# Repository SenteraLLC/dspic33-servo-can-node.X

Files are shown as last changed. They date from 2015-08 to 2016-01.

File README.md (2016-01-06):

# CAN Servo-Node

Initial development performed by partnership of [Sentera, LLC](https://sentera.com/) and [University of Minnesota](http://www.uav.aem.umn.edu/).

## System Overview
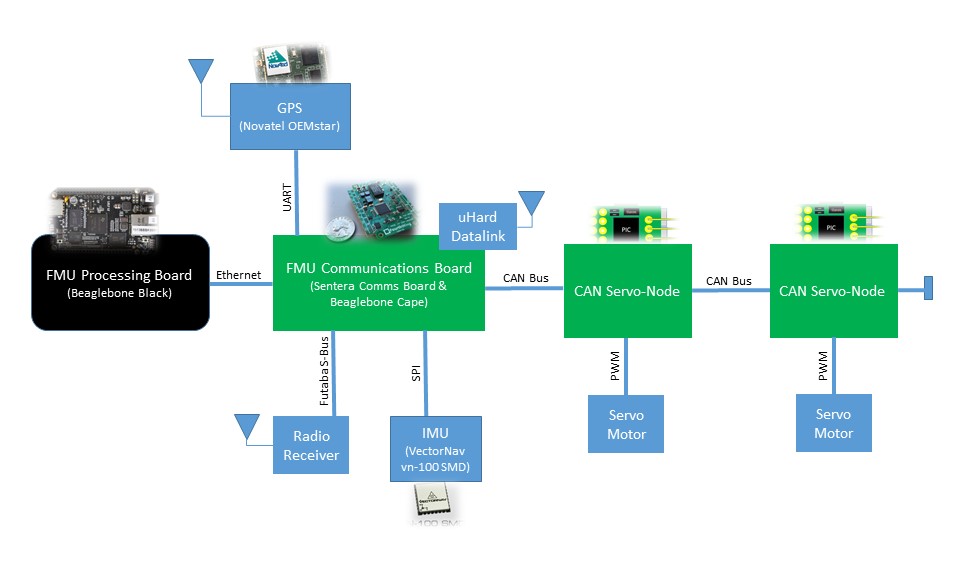
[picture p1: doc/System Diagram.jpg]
System Diagram


The CAN Servo-Node is designed as a component of the Flight Management System.  The CAN Servo-Node is a Microchip dsPIC33 based module with the primary function of receiving servo commands over a CAN bus, and controlling power to a servo based on those commands.  CAN communication is documented in file [UMN FMU Communication Protocol](https://github.com/SenteraLLC/pic32-fmu.X/blob/master/doc/UMN%20FMU%20Communication%20Protocol.docx).  When commanding the position of a servo, the software performs servo calibration correction so the required PWM value is applied to the servo.

Besides the described primary function, the CAN Servo-Node also:

* Performs monitoring of servo current and voltage, and annunciation of servo status on the CAN bus.

* Performs monitoring of VSENSE1 and VSENSE2 signals (described more below), calibration correction of values, and annunciation on the CAN bus.

* Provides reading and writing of calibration correction values (for the servo, VSENSE1, and VSENSE2) on the CAN bus.

The software design for the FMU Communications Board can be found at GitHub repository: [https://github.com/SenteraLLC/pic32-fmu.X](https://github.com/SenteraLLC/pic32-fmu.X).

## Project Folder Structure
The project includes the following folders:

>[doc](/doc) - documentation for the project.

>[doxygen](/doxygen) - project file for generating Doxygen documentation.

>[hw](/hw) - hardware design schematics.

>[inc](/inc) - include (i.e. header) code files.

>[ipe](/ipe) - instructions for a device programming method which maintains unique serial numbers.

>[nbproject](/nbproject) - MPLAB X IDE project files.

>[src](/src) – source code files.

## Hardware Overview
The hardware contains the following connectors:

>J1 - Servo voltage input (note: PWM input not currently used).

>J2 - Servo voltage and PWM output.

>J3 - Power (VCC/GND) and CAN connector.

>J4 - Duplicate Power (VCC/GND) and CAN connector.

>J5 - Power (VCC/GND) output and V_SENSE1 input.

>J6 - Power (VCC/GND) output and V_SENSE2 input.

The J3 or J4 connector is used to supply power to the CAN Servo-Node and to provide connection to the CAN bus.  The duplicate connector is used to continue wiring to additional devices (e.g. an additional CAN Servo-Node) or to provide termination of the CAN bus (i.e. terminating resistor).

The J5 and J6 connectors provide power to two additional devices.  These connectors also include an analog signal (V_SENSE1/2) which the CAN Servo-Node reads.  Likely devices connected to this interface include pressure sensors, temperature sensors, potentiometers, etc.

*Note: The CAN Servo-Node requires 5V supplied power (VCC) through the J3 or J4 connector.*

## Software Overview
All source code is commented using Doxygen style formatting.  Therefore, Doxygen can be used to generate an easily navigable document which provides greater detail into the software's operation than the overview which is provided here.

### Software Executive
The software implements a preemptive, cyclic executive using four threads.  The software threads are:

1. **Reset**: Thread is executed following reset.  Within the MPLAB environment this is implemented as "main" which provides C-environment control-flow entry.

2. **10ms**: Thread is executed every 10ms and provides the primary periodic software processing.

3. **0.1ms**: Thread is executed every 0.1ms and provides a granular time reference for determining relative time.

4. **Default**: Thread is executed if any unexpected interrupts occur.

The 'Reset' thread is executed out of reset and has the lowest priority.  The '10ms' thread has a priority of 1 and therefore can preempt the 'Reset' thread.  The '0.1ms' thread has a priority of 2 and therefore can preempt both the 'Reset' and '1ms' threads.

### Software Modules
The software is a modular design with no global data access.  The software modules are explained below, and map directly to [source code](/src) file names:

>**adc**: Analog to Digital Converter (ADC) driver.

>**can**: Controller Area Network (CAN) driver.

>**cfg**: Management of configuration data used by the software.  Note: configuration data is readable and writeable through the CAN interface.

>**dio**: Discrete I/O driver.

>**i2c**: Inter-Integrated Circuit (I2C) driver.

>**ina219**: External current/power monitor (INA219) driver.

>**main**: Software executive and C-environment control-flow entry.

>**nvm**: Non-Volatile Memory (NVM) driver.

>**osc**: Oscillator (OSC) driver.

>**pwm**: Pulse-Width Modulation (PWM) driver.

>**rst**: Reset condition detection.  The reset condition is annunciated over the CAN bus so unexpected resets can be identified.

>**servo**: Received CAN messages are processed to determine the servo control type - position or PWM control.  For position control, servo calibration correction is performed.  The determined PWM value is output to the servo and servo status CAN messages are periodically transmitted.

>**tmr**: Timer (TMR) driver.

>**util**: Utility functions.

>**ver**: Version and identification management. Version CAN messages are periodically transmitted to provide node identification.

>**vsense**: VSENSE1/2 signal management. The signals are calibration corrected and their value periodically annunciated in a CAN message.

>**wdt**: Watchdog Timer (WDT) driver.

## Building the Software
The recommended method for building the software is using tool [MPLAB X IDE](http://www.microchip.com/mplabx/) with compiler [MPLAB XC16](http://www.microchip.com/xc16/).  The IDE and compiler are both free software provided by Microchip.

*Note: v3.0 of MPLAB X IDE was used during development.*

*Note: v1.24 of MPLAB XC16 was used during development.*

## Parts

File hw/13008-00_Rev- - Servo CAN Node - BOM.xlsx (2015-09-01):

Production Quantity: | 25
Designator | Fitted | Comment | Manufacturer Part Number 1 | Manufacturer 1 | Description | Value | Quantity | Supplier 1 | Supplier Part Number 1 | Supplier Unit Price 1 | Supplier Order Qty 1 | Supplier Stock 1 | Delta Supplier 1 | Supplier Subtotal 1
C3, C4, C5, C7, C8, C9 | Fitted | C1005X7R1H104K | C1005X7R1H104K050BB | TDK Corporation | CAP CER 0.1UF 50V 10% X7R 0402 | 0.1uF | 6 | Digi-Key | 445-5932-1-ND | $0.05 | 150 | 7974509 | 7974359 | $7.12
C6 | Fitted | C1608X5R1A106M | C1608X5R1A106M080AC | TDK Corporation | CAP CER 10UF 10V X5R 20% 0603 | 10uF | 1 | Digi-Key | 445-6853-1-ND | $0.39 | 25 | 1201382 | 1201357 | $9.82
J1, J2 | Fitted | TSW-103-25-F-S-RA | TSW-103-25-F-S-RA | Samtec Inc | CONN HEADER 3POS .100" R/A AU |  | 2 | Digi-Key | TSW-103-25-F-SRA-ND | $0.46 | 50 | 0 | -50 | $23.00
J3, J4 | Fitted | 502386-0470 | 5023860470 | Molex Inc | CLIK-Mate CONN RCPT 4POS 1.25MM R/A SMD |  | 2 | Digi-Key | WM4948CT-ND | $0.96 | 50 | 3060 | 3010 | $48.23
J5, J6 | Fitted | 502386-0370 | 5023860370 | Molex Inc | CONN RCPT 3POS 1.25MM R/A SMD |  | 2 | Digi-Key | WM4947CT-ND | $0.88 | 50 | 1588 | 1538 | $44.07
J7 | Fitted | 502386-0570 | 5023860570 | Molex Inc | CLIK-Mate CONN RCPT 5POS 1.25MM R/A SMD |  | 1 | Digi-Key | WM4949CT-ND | $1.11 | 25 | 9764 | 9739 | $27.72
R2, R6, R8 | Fitted | ERJ-2RKF3300X | ERJ-2RKF3300X | Panasonic Electronic Components | RES 330 OHM 1/10W 1% 0402 SMD | 330 | 3 | Digi-Key | P330LCT-ND | $0.01 | 100 | 665642 | 665542 | $1.10
R3, R4 | Fitted | ERJ-2RKF3301X | ERJ-2RKF3301X | Panasonic Electronic Components | RES 3.30K OHM 1/10W 1% 0402 SMD | 3.3k | 2 | Digi-Key | P3.30KLCT-ND | $0.01 | 50 | 391761 | 391711 | $0.75
R5 | Fitted | ERJ-2RKF1002X | ERJ-2RKF1002X | Panasonic Electronic Components | RES 10.0K OHM 1/10W 1% 0402 SMD | 10k | 1 | Digi-Key | P10.0KLCT-ND | $0.01 | 50 | 13048611 | 13048561 | $0.75
R7 | Fitted | PMR10EZPFU8L00 | PMR10EZPFU8L00 | Rohm Semiconductor | RES SMD 0.008 OHM 1% 1/2W 0805 | .008 | 1 | Digi-Key | RHM.008AJCT-ND | $0.45 | 25 | 8069 | 8044 | $11.14
U1 | Fitted | SN65HVD1050DR | SN65HVD1050DR | Texas Instruments | IC EMC CAN TRANSCEIVER 8-SOIC |  | 1 | Digi-Key | 296-26335-1-ND | $1.03 | 25 | 11992 | 11967 | $25.75
U2 | Fitted | INA219BIDCNT | INA219BIDCNT | Texas Instruments | IC MONITOR PWR/CURR BID SOT-23-8 |  | 1 | Digi-Key | 296-27898-1-ND | $2.36 | 25 | 2367 | 2342 | $59.00
U3 | Fitted | KC5032A10.0000CMGE00 | KC5032A10.0000CMGE00 | AVX Corp/Kyocera Corp | OSCILLATOR XO 10.000MHZ CMOS SMD |  | 1 | Digi-Key | 1253-1284-1-ND | $1.49 | 25 | 1323 | 1298 | $37.30
U4 | Fitted | DSPIC33EV256GM102-I/MM | DSPIC33EV256GM102-I/MM | Microchip Technology | IC DSC 16BIT 16KB |  | 1 | Digi-Key | DSPIC33EV256GM102-I/MM-ND | $4.43 | 25 | 184 | 159 | $110.75
R1 | Not Fitted | ERJ-2RKF1200X | ERJ-2RKF1200X | Panasonic Electronic Components | RES 120 OHM 1/10W 1% 0402 SMD | 120 | 0 | Digi-Key | P120LCT-ND | $0.10 | 1 | 185622 | 185621 | $0.10
 |  |  |  |  |  |  | 25 |  |  |  |  |  |  | $406.61
 |  |  |  |  |  |  |  |  |  |  |  |  | Unit Cost | $16.26

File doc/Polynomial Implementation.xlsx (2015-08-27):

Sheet: Servo
 | Multiplier | Bit Shift
Coeff Mul | 100000000
Val Mul | 1000
Calc Mul | 1000000000
Out Mul | 1000000
Calc | 1073741824 | 30
 | 100
 | type | min supported | max supported |  | unit | Scale |  | decimal | integer (number) | integer (scientific)
c0 | int32_t | -2147483648 | 2147483647 |  | [s] |  | 1E8 | 0.00000000 | 0 | 0
c1 | int32_t | -2147483648 | 2147483647 |  | [s/rad^1] |  | 1E8 | 0.00100000 | 100000 | 100000
c2 | int32_t | -2147483648 | 2147483647 |  | [s/rad^2] |  | 1E8 | 0.00001600 | 1600 | 1600
c3 | int32_t | -2147483648 | 2147483647 |  | [s/rad^3] |  | 1E8 | 0.00000000 | 0 | 0
c4 | int32_t | -2147483648 | 2147483647 |  | [s/rad^4] |  | 1E8 | 0.00000000 | 0 | 0
c5 | int32_t | -2147483648 | 2147483647 |  | [s/rad^5] |  | 1E8 | 0.00000000 | 0 | 0
x | int16_t | -32768 | 32767 |  | [rad] |  | 1E3 | 0.25 | 250 | 250
x_calc | int64_t | -9.223372037e+18 | 9.223372037e+18 |  | [rad] |  | 2^30 | 0.250 | 268435456 | 268435456 |  | Up-scaled for calculation resolution.
x_calc^0 | int32_t | -2147483648 | 2147483647 |  |  |  | 2^30 | 1.000000000 | 1073741824 | 1073741824
x_calc^1 | int32_t | -2147483648 | 2147483647 |  | [rad^1] |  | 2^30 | 0.250000000 | 268435456 | 268435456
x_calc^2 | int32_t | -2147483648 | 2147483647 |  | [rad^2] |  | 2^30 | 0.062500000 | 67108864 | 67108864
x_calc^3 | int32_t | -2147483648 | 2147483647 |  | [rad^3] |  | 2^30 | 0.015625000 | 16777216 | 16777216
x_calc^4 | int32_t | -2147483648 | 2147483647 |  | [rad^4] |  | 2^30 | 0.003906250 | 4194304 | 4194304
x_calc^5 | int32_t | -2147483648 | 2147483647 |  | [rad^5] |  | 2^30 | 0.000976562 | 1048576 | 1048576
c0*x^0 | int64_t | -9.223372037e+18 | 9.223372037e+18 |  | [s] |  | 1E8 * 2^30 | 0.000000000 | 0 | 0
c1*x^1 | int64_t | -9.223372037e+18 | 9.223372037e+18 |  | [s] |  | 1E8 * 2^30 | 0.000250000 | 26843545600000 | 26843545600000
c2*x^2 | int64_t | -9.223372037e+18 | 9.223372037e+18 |  | [s] |  | 1E8 * 2^30 | 0.000001000 | 107374182400 | 107374182400
c3*x^3 | int64_t | -9.223372037e+18 | 9.223372037e+18 |  | [s] |  | 1E8 * 2^30 | 0.000000000 | 0 | 0
c4*x^4 | int64_t | -9.223372037e+18 | 9.223372037e+18 |  | [s] |  | 1E8 * 2^30 | 0.000000000 | 0 | 0
c5*x^5 | int64_t | -9.223372037e+18 | 9.223372037e+18 |  | [s] |  | 1E8 * 2^30 | 0.000000000 | 0 | 0
 |  |  |  |  |  |  |  |  | 25100
PWM | uint16_t | 0 | 65536 |  | [s] |  | 1E6 | 0.000251000 | 251 | 251
 |  |  |  | realterm
 |  |  |  |  |  |  |  | 16 |  |  | 2 | 8
 |  |  |  |  |  |  |  | 4 |  |  | *
 |  |  |  |  |  |  |  |  |  |  | 3 | 12
 |  |  |  |  |  |  |  |  |  |  |  | 96
 |  |  |  |  |  |  |  |  |  |  |  | 6

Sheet: VSENSE
 | Multiplier | Bit Shift
Val Mul | 262144 | 18
Coeff Mul | 10000
Calc | 1073741824 | 30 |  | Number represented in Q2.30 format (i.e. 30 fractional bits).
Out Mul | 100
 | type | min supported | max supported |  | Scale | Scale | decimal | integer (number) | integer (scientific)
c0 | int32_t | -2147483648 | 2147483647 |  | 1E4 | 10000 | 1.0000 | 10000 | 10000
c1 | int32_t | -2147483648 | 2147483647 |  | 1E4 | 10000 | 4.0000 | 40000 | 40000
c2 | int32_t | -2147483648 | 2147483647 |  | 1E4 | 10000 | 16.0000 | 160000 | 160000
c3 | int32_t | -2147483648 | 2147483647 |  | 1E4 | 10000 | 64.0000 | 640000 | 640000
c4 | int32_t | -2147483648 | 2147483647 |  | 1E4 | 10000 | 256.0000 | 2560000 | 2560000
c5 | int32_t | -2147483648 | 2147483647 |  | 1E4 | 10000 | 1024.0000 | 10240000 | 10240000
x | int16_t | -32768 | 32767 |  | 2^12 | 4096 | 0.2500000 | 1024 | 1024
x_calc | int32_t | -2147483648 | 2147483647 |  | 2^30 | 1073741824 | 0.2500000 | 268435456 | 268435456 | Up-scaled for calculation resolution.
x_calc^0 | int32_t | -2147483648 | 2147483647 |  | 2^30 | 1073741824 | 1.0000000 | 1073741824 | 1073741824
x_calc^1 | int32_t | -2147483648 | 2147483647 |  | 2^30 | 1073741824 | 0.2500000 | 268435456 | 268435456
x_calc^2 | int32_t | -2147483648 | 2147483647 |  | 2^30 | 1073741824 | 0.0625000 | 67108864 | 67108864
x_calc^3 | int32_t | -2147483648 | 2147483647 |  | 2^30 | 1073741824 | 0.0156250 | 16777216 | 16777216
x_calc^4 | int32_t | -2147483648 | 2147483647 |  | 2^30 | 1073741824 | 0.0039062 | 4194304 | 4194304
x_calc^5 | int32_t | -2147483648 | 2147483647 |  | 2^30 | 1073741824 | 0.0009766 | 1048576 | 1048576
c0*x^0 | int64_t | -9.223372037e+18 | 9.223372037e+18 |  | 1E4 * 2^30 | 10737418240000 | 1.0000000 | 10737418240000 | 10737418240000
c1*x^1 | int64_t | -9.223372037e+18 | 9.223372037e+18 |  | 1E4 * 2^30 | 10737418240000 | 1.0000000 | 10737418240000 | 10737418240000
c2*x^2 | int64_t | -9.223372037e+18 | 9.223372037e+18 |  | 1E4 * 2^30 | 10737418240000 | 1.0000000 | 10737418240000 | 10737418240000
c3*x^3 | int64_t | -9.223372037e+18 | 9.223372037e+18 |  | 1E4 * 2^30 | 10737418240000 | 1.0000000 | 10737418240000 | 10737418240000
c4*x^4 | int64_t | -9.223372037e+18 | 9.223372037e+18 |  | 1E4 * 2^30 | 10737418240000 | 1.0000000 | 10737418240000 | 10737418240000
c5*x^5 | int64_t | -9.223372037e+18 | 9.223372037e+18 |  | 1E4 * 2^30 | 10737418240000 | 1.0000000 | 10737418240000 | 10737418240000
Corrected | uint16_t | 0 | 65536 |  | 1E2 | 100 | 6.0000000 | 600 | 600

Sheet: Servo_position_conversion
input value | int | scaled | to base 2 | upscale to Q30 | output value | multi-factor | exact
0.980 | 980 | 2055208960 | 2055208 | 1052266496 | 0.9799995422 | 1073741.322 | 1073741.824
0.981 | 981 | 2057306112 | 2057306 | 1053340672 | 0.9809999466 | 1073741.766 | 1073741.824
0.982 | 982 | 2059403264 | 2059403 | 1054414336 | 0.9819998741 | 1073741.686 | 1073741.824
0.983 | 983 | 2061500416 | 2061500 | 1055488000 | 0.9829998016 | 1073741.607 | 1073741.824
0.984 | 984 | 2063597568 | 2063597 | 1056561664 | 0.9839997292 | 1073741.528 | 1073741.824
0.985 | 985 | 2065694720 | 2065694 | 1057635328 | 0.9849996567 | 1073741.45 | 1073741.824
0.986 | 986 | 2067791872 | 2067791 | 1058708992 | 0.9859995842 | 1073741.371 | 1073741.824
0.987 | 987 | 2069889024 | 2069889 | 1059783168 | 0.9869999886 | 1073741.812 | 1073741.824
0.988 | 988 | 2071986176 | 2071986 | 1060856832 | 0.9879999161 | 1073741.733 | 1073741.824
0.989 | 989 | 2074083328 | 2074083 | 1061930496 | 0.9889998436 | 1073741.654 | 1073741.824
0.990 | 990 | 2076180480 | 2076180 | 1063004160 | 0.9899997711 | 1073741.576 | 1073741.824
0.991 | 991 | 2078277632 | 2078277 | 1064077824 | 0.9909996986 | 1073741.497 | 1073741.824
0.992 | 992 | 2080374784 | 2080374 | 1065151488 | 0.9919996262 | 1073741.419 | 1073741.824
0.993 | 993 | 2082471936 | 2082471 | 1066225152 | 0.9929995537 | 1073741.341 | 1073741.824
0.994 | 994 | 2084569088 | 2084569 | 1067299328 | 0.993999958 | 1073741.779 | 1073741.824
0.995 | 995 | 2086666240 | 2086666 | 1068372992 | 0.9949998856 | 1073741.701 | 1073741.824
0.996 | 996 | 2088763392 | 2088763 | 1069446656 | 0.9959998131 | 1073741.622 | 1073741.824
0.997 | 997 | 2090860544 | 2090860 | 1070520320 | 0.9969997406 | 1073741.545 | 1073741.824
0.998 | 998 | 2092957696 | 2092957 | 1071593984 | 0.9979996681 | 1073741.467 | 1073741.824
0.999 | 999 | 2095054848 | 2095054 | 1072667648 | 0.9989995956 | 1073741.389 | 1073741.824
1.000 | 1000 | 2097152000 | 2097152 | 1073741824 | 1 | 1073741.824 | 1073741.824
45.000 | 45000 | 94371840000 | 94371840 | 48318382080 | 45 | 1073741.824 | 1073741.824

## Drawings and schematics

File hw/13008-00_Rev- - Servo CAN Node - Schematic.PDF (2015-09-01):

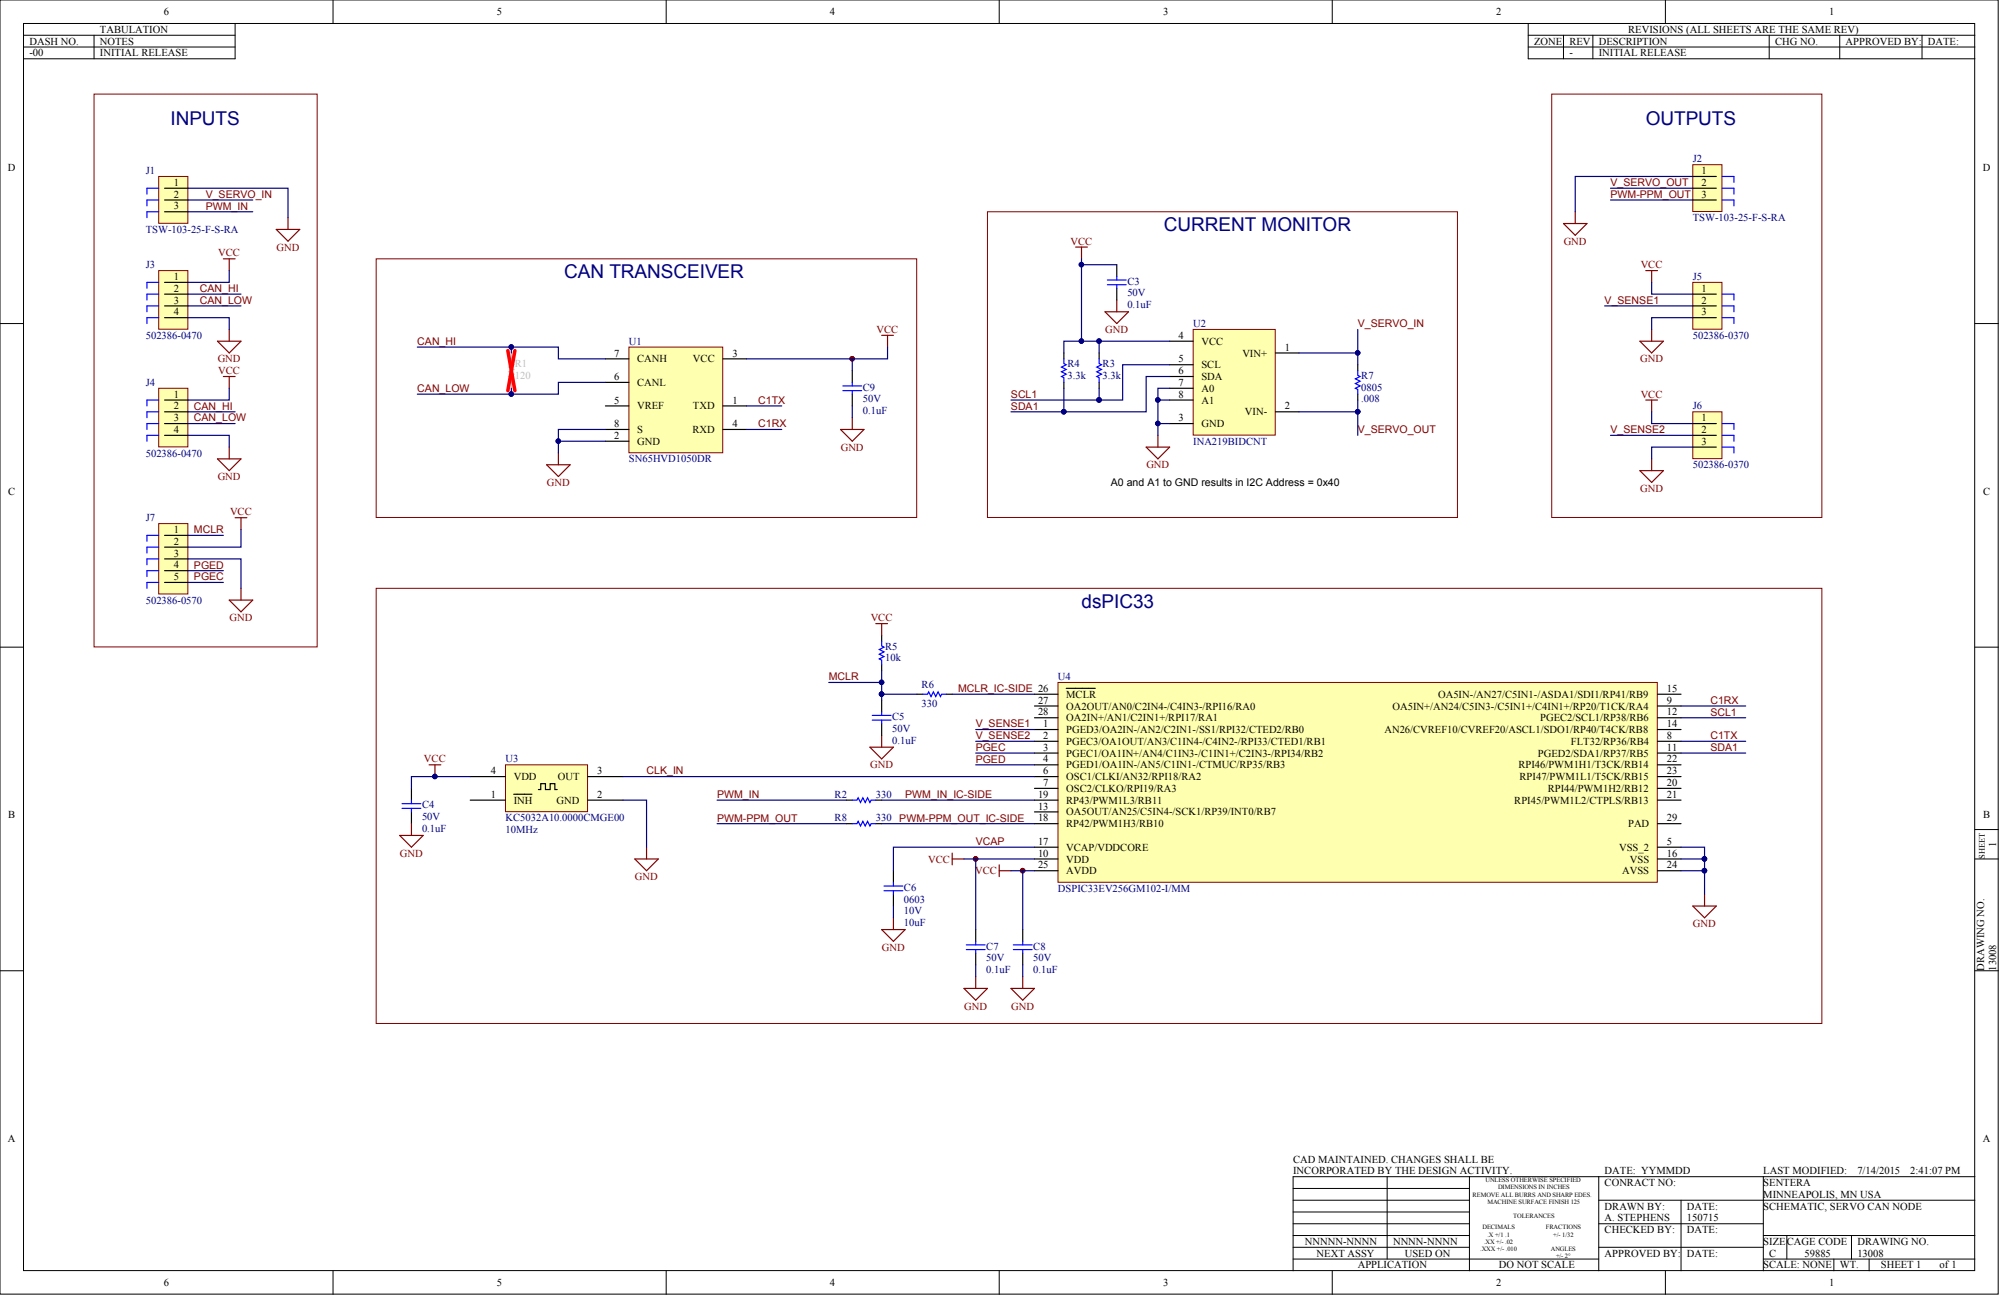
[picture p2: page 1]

REVISIONS (ALL SHEETS ARE THE SAME REV)

CAN_LOW | 5

A0 and A1 to GND results in I2C Address = 0x40

CAD MAINTAINED. CHANGES SHALL BE
INCORPORATED BY THE DESIGN ACTIVITY.

LAST MODIFIED: 7/14/2015 2:41:07 PM
SENTERA
MINNEAPOLIS, MN USA
SCHEMATIC, SERVO CAN NODE

VE ALL BURRS AN
ACHINE S

CHECKED BY: | DATE:

NNNNN-NNNN | NNNN-NNNN
NEXT ASSY | USED ON

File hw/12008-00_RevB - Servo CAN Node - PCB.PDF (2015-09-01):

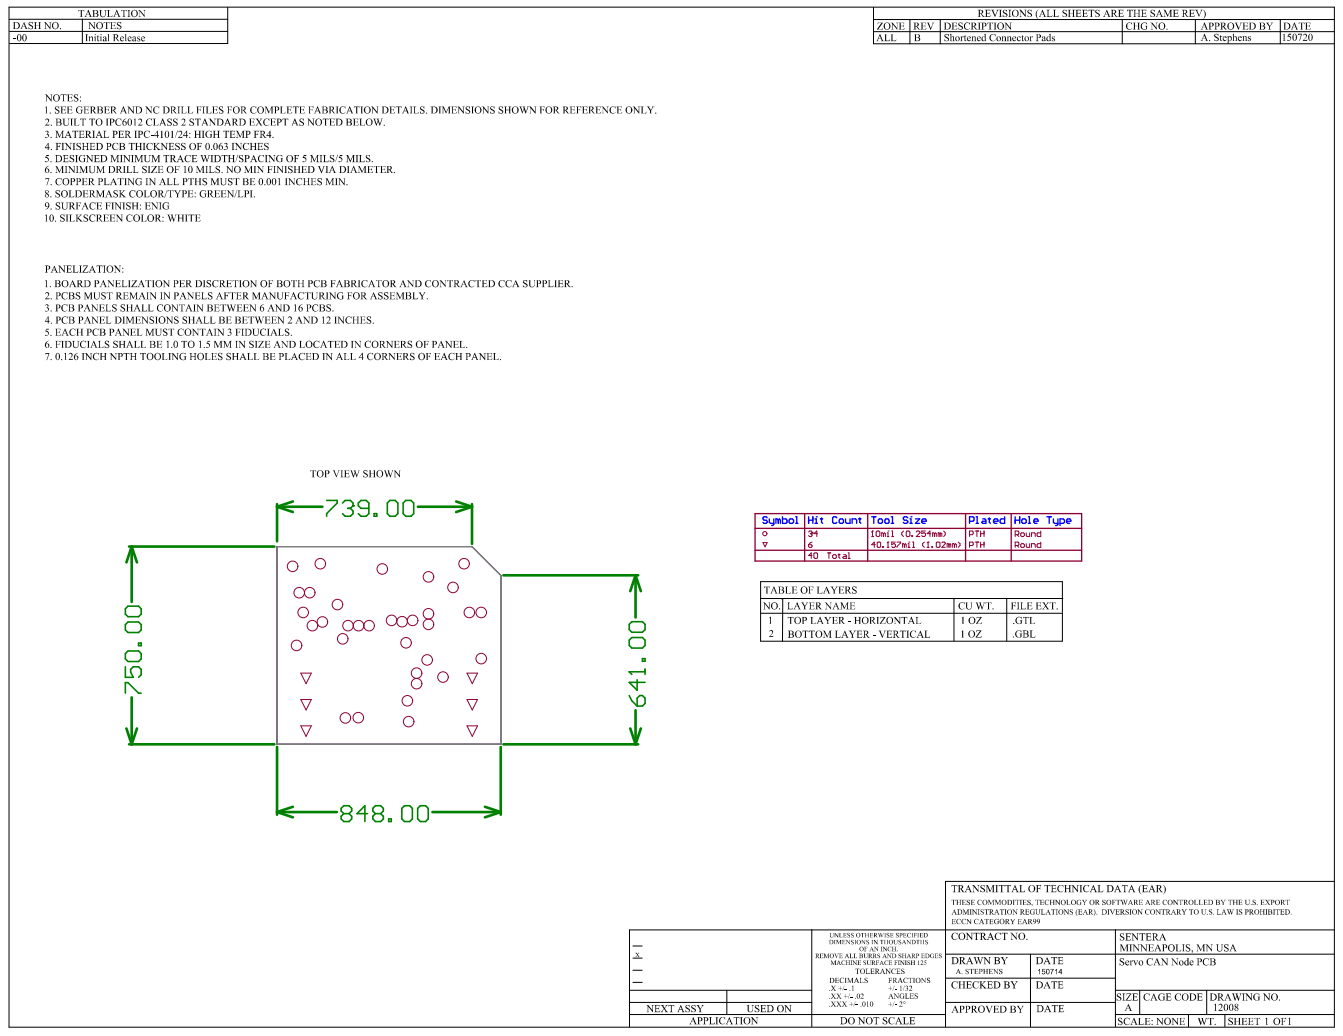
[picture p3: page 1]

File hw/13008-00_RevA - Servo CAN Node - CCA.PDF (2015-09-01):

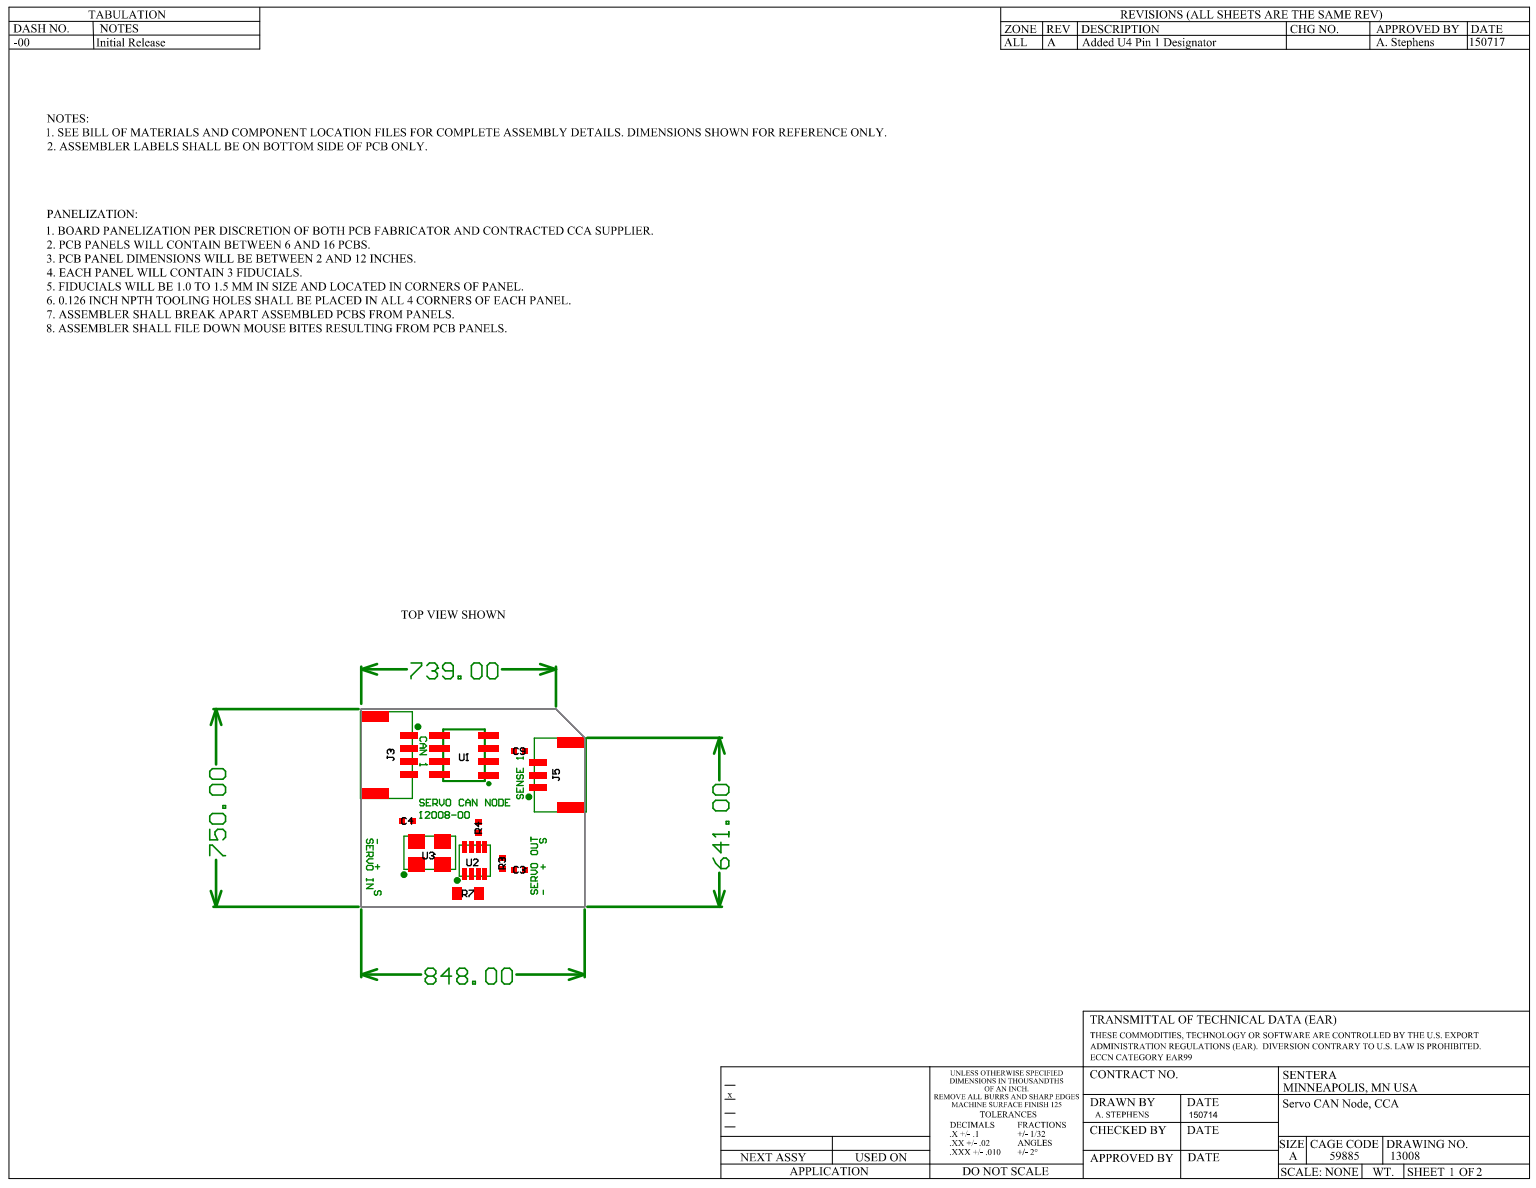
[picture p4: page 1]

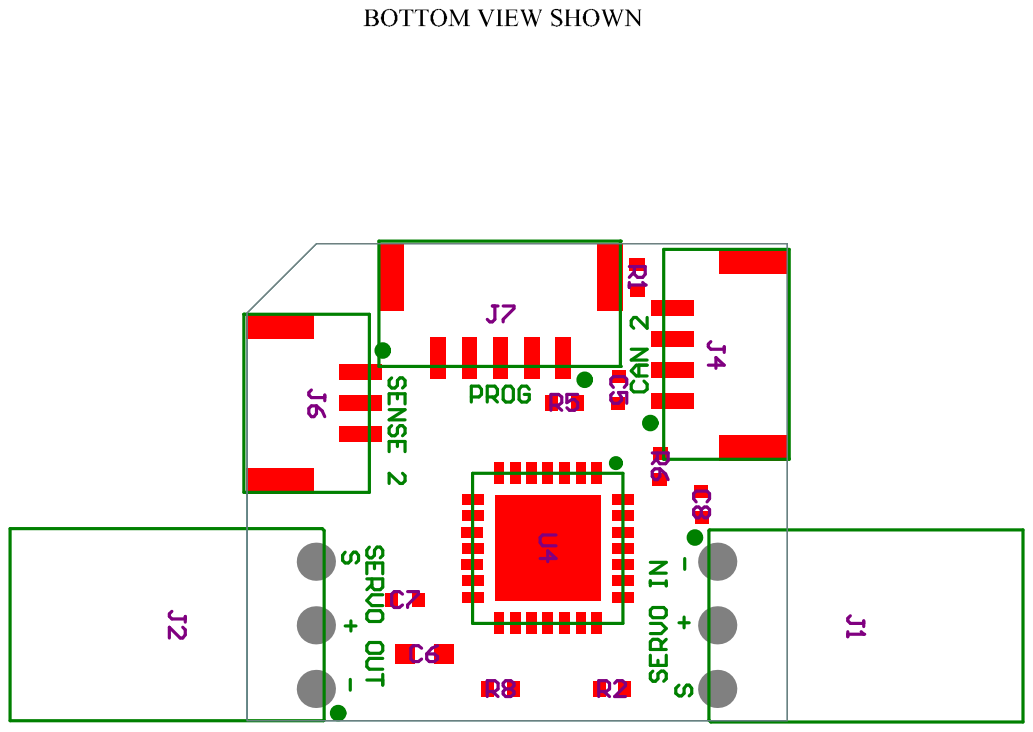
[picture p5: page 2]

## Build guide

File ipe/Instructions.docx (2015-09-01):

# Overview

This document details the use of software tool MPLAB® Integrated Programming Environment (IPE) for programming CAN Servo-Nodes. The IPE provides a method to perform programming and serial number control of embedded software. The IPE is a free tool, which is downloaded along with the MPLAB IDE or can be downloaded independently (http://microchip.wikidot.com/ipe:installation).

Steps listed below as “optional” are needed if a unique serial number for each CAN Servo-Node is desired. The IPE maintains a Serialized Quick Turn Programming (SQTP) file for recording used and available serial numbers. This SQTP file is updated by the IPE tool during the programming operation to identify that a serial number was used to program a target. The SQTP file must be maintained within a Version Control System (VCS) to guarantee that unique serial numbers are maintained for different target devices.

Different sections exist below for ‘initial programming’ and ‘reprogramming’. The difference exists because the serial number is programmed during initial programming, and then preserved within non-volatile memory when reprogramming the device. If unique serial numbers are not required the ‘initial programming’ steps can always be performed, even when reprogramming a device.

# Initial Programming Steps

1. Open the MPLAB IPE tool.
2. Select: Settings >> Advanced Mode.
3. Enter password (‘microchip’ is default) and press: Log on.
4. On the left side of the Screen, select: Operate.
5. From the “Family” drop-down, select: 16-bit DSCs (dsPIC33).
6. From the “Device” drop-down, select: dsPIC33EV256GM102.
7. From the “Tool” drop-down, select the programming tool being used to program the target.
8. Click the button: Apply.
9. Click the button: Connect.
10. If presented with the cautionary pop-up window on device voltage, select: Yes.
11. To the right of the “Source” label select button: Browse.
12. Navigate to and select the required file to download to the target, for example: C:\Users\Jon Watson\Documents\GitHub\dspic33-servo-can-node.X\dist\default\production\dspic33-servo-can-node.X.production.hex
13. (optional) To the right of the “SQTP” label select button: Browse.
14. (optional) Select the SQTP file which includes serial number information, for example: C:\Users\Jon Watson\Documents\GitHub\dspic33-servo-can-node.X\ipe\DSPIC33EV256GM102_SQTP.num
15. Program the target by selecting button: Program.
16. (optional) Update the SQTP file within a selected VCS.

The initial programming operation is complete. The below figure provides an example screenshot of the MPLAB IPE tool following the programming steps being completed:

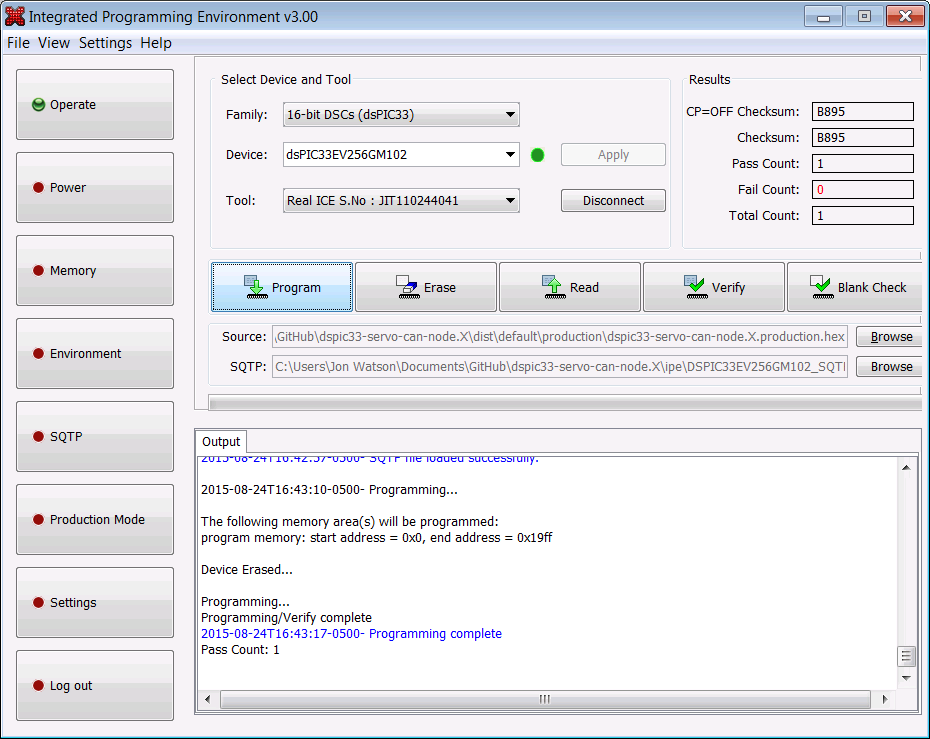
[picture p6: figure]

# Reprogramming Steps (optional)

1. Open the MPLAB IPE tool.
2. Select: Settings >> Advanced Mode.
3. Enter password (‘microchip’ is default) and press: Log on.
4. On the left side of the Screen, select: Memory.
5. In the “Preserve Memory” section, check the check-box: Preserve Flash on Program.
6. Select for a “Start Address”: 0x200.
7. Select for an “End Address”: 0x2FF.
8. On the left side of the Screen, select: Operate.
9. From the “Family” drop-down, select: 16-bit DSCs (dsPIC33).
10. From the “Device” drop-down, select: dsPIC33EV256GM102.
11. From the “Tool” drop-down, select the programming tool being used to program the target.
12. Click the button: Apply.
13. Click the button: Connect.
14. If presented with the cautionary pop-up window on device voltage, select: Yes.
15. To the right of the “Source” label select button: Browse.
16. Navigate to and select the required file to download to the target, for example: C:\Users\Jon Watson\Documents\GitHub\dspic33-servo-can-node.X\dist\default\production\dspic33-servo-can-node.X.production.hex
17. Program the target by selecting button: Program.

The reprogramming operation is complete. The below figure provides an example screenshot of the MPLAB IPE tool following the programming steps being completed (Note: from the “Output” window it can be verified that the expected memory range was preserved):

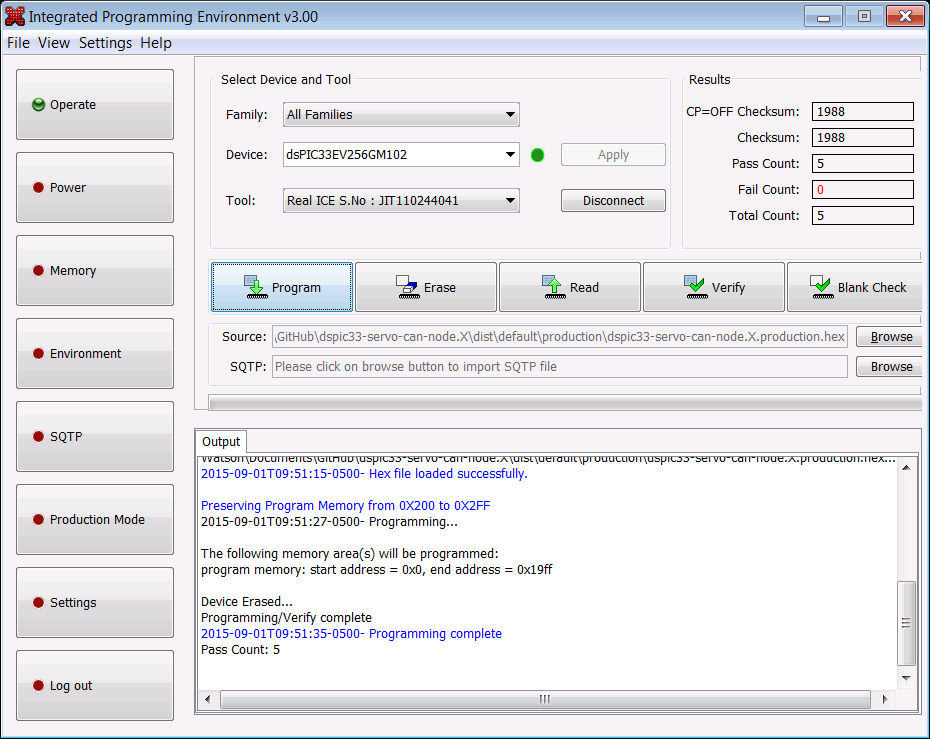
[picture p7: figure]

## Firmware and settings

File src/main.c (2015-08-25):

////////////////////////////////////////////////////////////////////////////////
/// @file   
/// @brief  Executive control-flow.
////////////////////////////////////////////////////////////////////////////////

// *****************************************************************************
// ************************** System Include Files *****************************
// *****************************************************************************

#include <xc.h>
#include <stdbool.h>
#include <stddef.h>
#include <stdint.h>

// *****************************************************************************
// ************************** User Include Files *******************************
// *****************************************************************************

#include "adc.h"
#include "can.h"
#include "cfg.h"
#include "dio.h"
#include "i2c.h"
#include "ina219.h"
#include "nvm.h"
#include "osc.h"
#include "pwm.h"
#include "rst.h"
#include "servo.h"
#include "tmr.h"
#include "ver.h"
#include "vsense.h"
#include "wdt.h"

// *****************************************************************************
// ************************** Defines ******************************************
// *****************************************************************************

// DSPIC33EV256GM102 Configuration Bit Settings
// FSEC
#pragma config BWRP     = OFF           // Boot Segment Write-Protect Bit (Boot Segment may be written)
#pragma config BSS      = DISABLED      // Boot Segment Code-Protect Level bits (No Protection (other than BWRP))
#pragma config BSS2     = OFF           // Boot Segment Control Bit (No Boot Segment)
#pragma config GWRP     = OFF           // General Segment Write-Protect Bit (General Segment may be written)
#pragma config GSS      = DISABLED      // General Segment Code-Protect Level bits (No Protection (other than GWRP))
#pragma config CWRP     = OFF           // Configuration Segment Write-Protect Bit (Configuration Segment may be written)
#pragma config CSS      = DISABLED      // Configuration Segment Code-Protect Level bits (No Protection (other than CWRP))
#pragma config AIVTDIS  = DISABLE       // Alternate Interrupt Vector Table Disable Bit  (Disable Alternate Vector Table)

// FBSLIM
// Note: Register is not explicitely set.  Definition of serial number in 
// Program Memory at specific address causes compiler warning when BSLIM is
// also set (even through the Boot Segment is not used - see BSS2).  Therefore,
// FBSLIM will be its default value.

// FOSCSEL
#pragma config FNOSC    = PRIPLL        // Initial oscillator Source Selection Bits (Primary Oscillator with PLL module (XT + PLL, HS + PLL, EC + PLL))
#pragma config IESO     = OFF           // Two Speed Oscillator Start-Up Bit (Start up device with user selected oscillator source)

// FOSC
#pragma config POSCMD   = EC            // Primary Oscillator Mode Select Bits (EC (External Clock) mode)
#pragma config OSCIOFNC = ON            // OSC2 Pin I/O Function Enable Bit (OSC2 is general purpose digital I/O pin)
#pragma config IOL1WAY  = ON            // Peripheral Pin Select Configuration Bit (Allow Only One reconfiguration)
#pragma config FCKSM    = CSDCMD        // Clock Switching Mode Bits (Both Clock Switching and Fail-safe Clock Monitor are disabled)
#pragma config PLLKEN   = ON            // PLL Lock Enable Bit (Clock switch to PLL source will wait until the PLL lock signal is valid)

// FWDT - Configuration Register
//
// WDT source is a low-power RC (LPRC) oscillator with nominal frequency 
// (Flprc) of 32kHz.
//
// Twto := Watchdog time-out period
//
// Twto =   Tlprc * WDTPRE * WDTPOST
//      = 31.25us *     32 *      32
//      =    32ms
//
// Note: Flprc accuracy is +-15% (see datasheet); therefore, selection of 32ms 
// nominal time-out period results in a minimum time-out period of ~27ms.
//
#pragma config WDTPOST  = PS32          // Select WDT postscaler = 32.
#pragma config WDTPRE   = PR32          // Select SDT prescaler = 32.
#pragma config FWDTEN   = ON_SWDTEN     // WDT disabled by default. WDT enabled in software.
#pragma config WINDIS   = OFF           // Operate WDT in Non-Window Mode.
#pragma config WDTWIN   = WIN25         // N/A - b/c of 'WINDIS' setting.

// FPOR
#pragma config BOREN0   = ON            // Brown Out Reset Detection Bit (BOR is Enabled)

// FICD
#pragma config ICS      = PGD1          // ICD Communication Channel Select Bits (Communicate on PGEC1 and PGED1)

// FDMTINTVL
#pragma config DMTIVTL  = 0xFFFF        // Lower 16 Bits of 32 Bit DMT Window Interval (Lower 16 bits of 32 bit DMT window interval (0-0xFFFF))

// FDMTINTVH
#pragma config DMTIVTH  = 0xFFFF        // Upper 16 Bits of 32 Bit DMT Window Interval (Upper 16 bits of 32 bit DMT window interval (0-0xFFFF))

// FDMTCNTL
#pragma config DMTCNTL  = 0xFFFF        // Lower 16 Bits of 32 Bit DMT Instruction Count Time-Out Value (Lower 16 bits of 32 bit DMT instruction count time-out value (0-0xFFFF))

// FDMTCNTH
#pragma config DMTCNTH  = 0xFFFF        // Upper 16 Bits of 32 Bit DMT Instruction Count Time-Out Value (Upper 16 bits of 32 bit DMT instruction count time-out value (0-0xFFFF))

// FDMT
#pragma config DMTEN    = DISABLE       // Dead Man Timer Enable Bit (Dead Man Timer is Disabled and can be enabled by software)

// FDEVOPT
#pragma config PWMLOCK  = OFF           // PWM Lock Enable Bit (Certain PWM registers may only be written after key sequence)
#pragma config ALTI2C1  = OFF           // Alternate I2C1 Pins Selection Bit (I2C1 mapped to SDA1/SCL1 pins)

// FALTREG
#pragma config CTXT1    = NONE          // Interrupt Priority Level (IPL) Selection Bits For Alternate Working Register Set 1 (Not Assigned)
#pragma config CTXT2    = NONE          // Interrupt Priority Level (IPL) Selection Bits For Alternate Working Register Set 2 (Not Assigned)

// *****************************************************************************
// ************************** Definitions **************************************
// *****************************************************************************

// *****************************************************************************
// ************************** Function Prototypes ******************************
// *****************************************************************************

// *****************************************************************************
// ************************** Global Functions *********************************
// *****************************************************************************

////////////////////////////////////////////////////////////////////////////////
/// @brief  C-Environment control-flow entry.
///
/// @return Zero is returned if function exits.
///
/// @note   Function implements an infinite loop, therefore function return
///         is not expected.
////////////////////////////////////////////////////////////////////////////////
int main ( void )
{
    // Enable the watchdog timer operation.
    WDTEnable();
    
    // Initialize CPU hardware.
    OSCInit();
    TMRInit();
    DIOInit();
    ADCInit();
    PWMInit();
    CANInit();
    NVMInit();
    I2CInit();
    
    // Initialize peripheral hardware.
    INA219Init();
    
    // Determine the processor reset source.
    RSTStartup();
    
    // Enable the hardware timer(s) to start interrupt thread(s) of main
    // processing control-flow.
    //
    // PWM is enabled at same time as interrupt timer(s) so that PWM cycle
    // is synchronized with processing cycle.  This is not required, but
    // yields a more deterministic design which yields easier identification
    // of the effect of the PWM control on the PWM applied.
    //
    TMR1Enable();
    PWMEnable();
    
    // Enable the Global Interrupt flag for executive control-flow.
    INTCON2bits.GIE = 1;
    
    // Execute background thread infinite-loop.
    while( 1 );
    
    return 0;
} 

////////////////////////////////////////////////////////////////////////////////
/// @brief  Main processing thread (10ms period).
///
/// This interrupt serves as the primary processing thread and is triggered
/// by the Timer1 10ms interrupt.  Interrupt priority is configured as '1', so
/// that the interrupt will preempt background thread execution.
////////////////////////////////////////////////////////////////////////////////
void __interrupt( no_auto_psv ) _T1Interrupt ( void )
{    
    // INPUT - Aquire input signals for software cycle execution.
    ADCService();
    INA219Service();
    
    // PROCESS & OUTPUT - Perform processing and output signals for software
    // cycle execution.
    WDTService();
    VsenseService();
    ServoService();
    CfgService();
    RSTService();
    VerService();
    
    // Service the timer 1 interrupt.
    TMR1Service();
}

////////////////////////////////////////////////////////////////////////////////
/// @brief  System timer update (0.1ms period)
///
/// This interrupt serves to update the system time and is triggered by the
/// Timer2 0.1ms interrupt.  Interrupt priority is configured as '2', so that
/// the interrupt will preempt background thread and T1Interrupt thread
/// execution.
////////////////////////////////////////////////////////////////////////////////
void __interrupt( no_auto_psv ) _T2Interrupt ( void )
{
    // Service the timer 2 interrupt.
    TMR2Service();
}

////////////////////////////////////////////////////////////////////////////////
/// @brief  Unused ISR trap.
///
/// ISR executes an infinite loop so that the WDT will reset the processor.
////////////////////////////////////////////////////////////////////////////////
void __interrupt( no_auto_psv ) _DefaultInterrupt ( void )
{
    while( 1 );
}

// *****************************************************************************
// ************************** Static Functions *********************************
// *****************************************************************************

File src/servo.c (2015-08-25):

////////////////////////////////////////////////////////////////////////////////
/// @file
/// @brief Servo management.
////////////////////////////////////////////////////////////////////////////////

// *****************************************************************************
// ************************** System Include Files *****************************
// *****************************************************************************

// *****************************************************************************
// ************************** User Include Files *******************************
// *****************************************************************************

#include "servo.h"
#include "ina219.h"
#include "can.h"
#include "cfg.h"
#include "util.h"
#include "pwm.h"

// *****************************************************************************
// ************************** Defines ******************************************
// *****************************************************************************

// Scaling factors for servo correction polynomial fields:
//
// - Coefficient scale      = 1E8 - ( i.e. LSB = 0.01  us/rad^x ).
// - PWM input scale        = 1E3 - ( i.e. LSB = 0.001 rad      ).
// - PWM output scale       = 1E6 - ( i.e. LSB = 1.0   us       ).
//
// Rationale:
//  The polynomial equation is implemented using fixed-point math since the 
//  hardware does not natively support floating-point arithmetic and the 
//  execution time of a floating-point implementation exceeds that available
//  for the calculation resolution required (i.e. double-precision).
//
//  Additionally, base2 fixed-point math is used rather than base10 as 
//  64-bit division is required and the time required for a base10 
//  implementation (i.e. integer division rather than bit-shift) exceeds
//  the processing time available.
//
// -----------------------------------------------------------------------------
//
// SERVO_QNUM_CALC:
//  The servo position command is up-scaled for resolution on internal 
//  calculation.  This is critical for maintained accuracy through the power
//  terms (e.g. pos^5) of the polynomial equation.
//
// SERVO_PWM_DIV:
//  The output of the polynomial equation has a scaling based on the 
//  coefficient scaling (i.e. 1E8).  The output is  down-scaled to remove the 
//  input scaling, and get the result term to the required units 
//  (i.e. 1E8 / 1E6 = 1E2).
//
// -----------------------------------------------------------------------------
//
#define SERVO_QNUM_CALC      30U        ///< Polynomial calculation Q-number.
#define SERVO_PWM_OUT_DIV   100U        ///< Post-calculation division factor.

// Values for scaling the PWM input to Q30 representation.
#define SERVO_PWM_IN_SHIFT1       21U   ///< Input position 1st l-shift (for Q30 scaling).
#define SERVO_PWM_IN_DIV        1000U   ///< Input position division (for Q30 scaling).
#define SERVO_PWM_IN_SHIFT2        9U   ///< Input position 2nd l-shift (for Q30 scaling).

/// List of servo control/command types.
typedef enum
{
    SERVO_CTRL_PWM,     ///< Servo controlled with PWM command.
    SERVO_CTRL_POS      ///< Servo controlled with position command.
    
} SERVO_CTRL_TYPE_E;

// *****************************************************************************
// ************************** Definitions **************************************
// *****************************************************************************

/// The command type used to control the servo.
///
/// @note   Default to PWM control.
static SERVO_CTRL_TYPE_E servo_cmd_type = SERVO_CTRL_PWM;

/// The PWM commanded value for servo control.
///
/// @note   Default to 1500us - i.e. neutral position.
static uint16_t servo_cmd_pwm = 1500;

/// The position commanded value for servo control.
///
/// @note   Default to 0.0 radians.
static int16_t servo_cmd_pos = 0;

/// The actual PWM value applied to the servo.
///
/// @note   Updated on execution of module service function.
static uint16_t servo_act_pwm;

// *****************************************************************************
// ************************** Function Prototypes ******************************
// *****************************************************************************

// *****************************************************************************
// ************************** Global Functions *********************************
// *****************************************************************************
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

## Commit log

2015-05-04 Initialized I2C parameters.
2015-07-08 Updated CAN definition error.
    [can.c]
2015-07-08 Updated CAN to 1Mbps. Data is observed using USB2CAN after addition of CAN bus termination resistor.
2015-07-08 CAN header construction fix.
    1. Updated mapping for population of CAN header fields to be correct.
    2. Updated identifier names to more concise, as they map between CAN
    header fields and hardware registers.
    [can.c]
2015-07-24 Integration testing updates.
    Corrected issues identified during integration testing. Larger
    corrections include:
    1. Update of CAN message rated to be slower than software cycle.
    2. Disabling lock of PWM configuration bits, since unlock sequence is
    not working and PWM registers are not safety critical - i.e. output
    would not yield electrical failure.
    3. Updated calibration correction coefficient values to have default
    scaling which makes verification of output possible.
    [can.c, cfg.c, main.c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]
2015-08-27 Addition of implementation detail on calibration polynomial calculation.
    [Polynomial Implementation.xlsx]
2015-09-01 Updated to perserve Serial Number through reprogramming. Updated programming instruction for reprogramming a device.
2015-09-01 Added hardware build files to "hw" folder.
    [12008-00_RevB - Servo CAN Node.GBL, 12008-00_RevB - Servo CAN Node.GBO, 12008-00_RevB - Servo CAN Node.GBP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]
